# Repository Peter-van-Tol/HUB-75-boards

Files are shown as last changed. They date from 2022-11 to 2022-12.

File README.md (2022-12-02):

# HUB-75 boards

The HUB-75 boards is a collection of break-out boards (BOBs) for HUB-75 connnectors found on re-purposed FPGA cards such as the 5A-75B and 5A-75E. These cards can be picked up for 10\~20 dollars from China and form an ideal basis for tinkering with FPGAs. Based on these cheap FPGA's a project has been spraked, called Litex-CNC, which aims to repurpose these cards to a cheap CNC controller. CNC-machines normally have field power which is 12\~24V and thus the FPGA cannot direclty be connected to the components of the machine. Therefore a set of break-out boards have been developed for GPIO inputs/outputs, stepgen, encoders, etc.

## Design philosophy
> Why not a hat one might ask? This project offers more flexibility. By combining different break-out can be combined to suit the machine that is being built. A hat also comes with a larger risk in design errors; smaller boards are easier to design, produce and check.

All BOBs will have the same dimensions of 85 mm x 56 mm. This size is equal to that of the Raspberry Pi 4, however the mounting holes are placed on the four corners and thus different from the RPi. Getting the mounting holes at the same location as the RPi made the design much more difficult. Placement of the connectors also hampers stacking these boards on top of each other, so not being to able to stack them on top of a RPi seems permissible.

The outputs of the BOBs will be on the bottom edge (long side). Field power and logic power are provided from the left side of the board. The HUB-75 connectors will be placed on the top of the boards. This makes it easier to route the digital signals and high-power signals separately from each other in the cabinet.

The smalles trace and spacing is 0.2 mm. These boards are designed to be ordered from an online PCB manufacturer. Some desktop milling machines might have the accuracy to create these traces, so you might give it a try when you are feeling lucky. The smallest holes (vias) are 0.3 mm in size.

All components are selected to be hand-solderable. This means that the following minimum sizes SMD components will be used:
- resistors, LED's, capacitors: SMD-1206
- diodes: SOD-123
- FET, transistors: SOT-23

## HUB-75 pinout
Each connector has 6 individual pins (1, 2, 3, 5, 6, and 7) and 8 shared pins (8 through 15). The standard pin-out of a HUB-75 connector is shown below.

| HUB75 pin | Pin | Pin | HUB75 pin |
|---|---|---|---|
| R0 | 1 | 2 | G0 |
| B0 | 3 | 4 | *GND* |
| R1 | 5 | 6 | G1 |
| B1 | 7 | 8 | E |
| A | 9 | 10 | B |
| C | 11 | 12 | D |
| CLK | 13 | 14 | STB |
| OE | 15 | 16 | *GND* |

Each HUB-75 connector will use the individual pins and in special cases one of the shared pins. In the design it should be taken into account that boards which uses the same shared pins might be mutual exclusive when the functions are different (different types of stepgen BOBs can off course be combined.

## Available BOBs
The table below shows the BOBs which are currently available in this repository, along with their status.

| Category  | Name | Description | HUB-75 | Status |
|---|---|---|---|---|
| stepgen | [HUB75-Differential_stepgen](HUB75-Differential_stepgen) | 3 differential stepgen channels, frequency up to 400 kHz | 2 + 0.5 | Prototype-2 ordered | 
| GPIO-out  | [HUB75-Sourcing_output](HUB75-Sourcing_output) | 12 channel sourcing output (<1 kHz, 4 A per channel, 4 A total) | 2 | Prototype-2 ordered | 
| GPIO-in | [HUB75-Sinking_input](HUB75-Sinking_input) | 12 channel sinking input (< 1 kHz) | 2 | Untested |

## Connecting the BOBs to your FPGA
On both the 5A-75B and the 5A-75E the `74HC245T` buffers are hard-wired as outputs. To be able to use the HUB-75 boards which require an input (as seen from the FPGA) some modifications on the board are required. Of both boards different versiosn exist, so the components can be at a different location on your board. Below are the locations of the buffer on a 5A-75B V6.1 (front) and 5A-75E V6.0 (back).

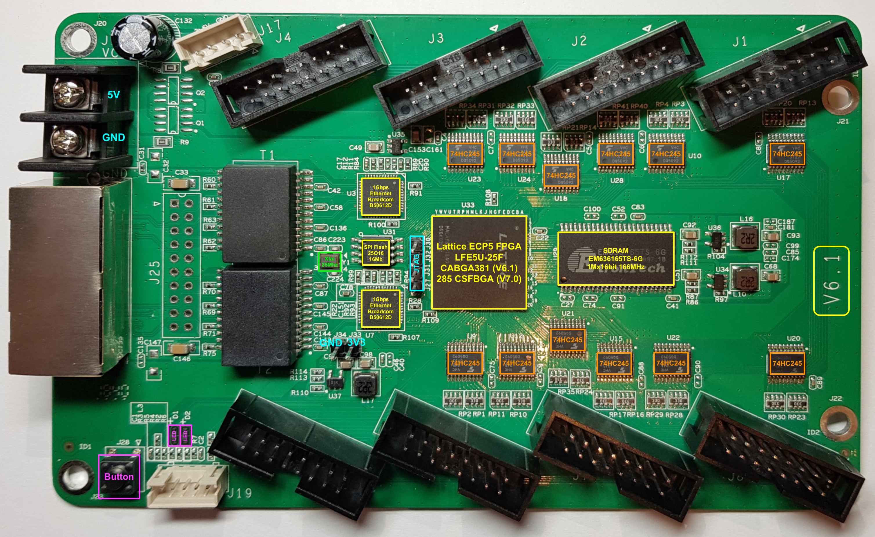
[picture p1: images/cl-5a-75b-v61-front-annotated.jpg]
5A-75B V6.1


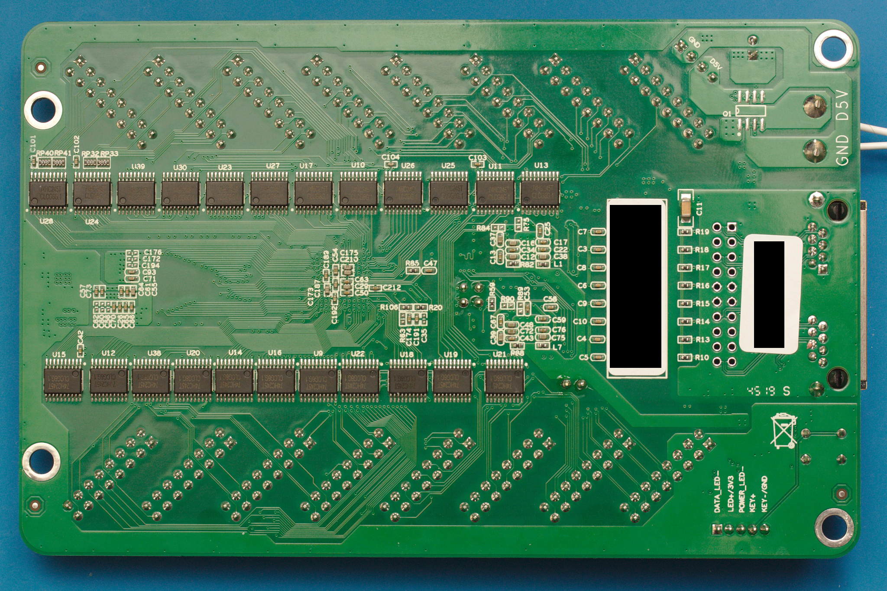
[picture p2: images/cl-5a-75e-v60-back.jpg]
5A-75E V6.0


Each buffer has 8 channels, while every HUB-75 connector has 6 individual pins. When you replace a buffer you will cahnge the behavior of one HUB-75 connector and partly that of its neighbor. All HUB-75 boards assume that a connector is either fully configured as input or as output. Therefore it is recommended to change the buffers direclty adjacent to each other, so the minimum amount of available connectors (partly input/ouput) are wasted.

The following changes have to be made to the buffers:
* De-solder the `74HC245T` buffer, this buffer cannot be re-used because its pins are not 5 Volt tolerant when `Vcc` is 3.3 Volt.
* Cut the trace to the pin `Vcc` (pin 20) and wire it to a 3.3V source (for example the JTAG-header). If you don't do this, a buffer configure as input will put 5 Volts on the pins of the FPGA, which will definately fry that pin or the whole board.
* Cut the trace to the pin `DIR` (pin 20) and wire it to a GND source to configure the buffer as input.
* Replace the buffer with a buffer with 5V tolerant inputs, such as the `74LVC245` ([datasheet](https://www.ti.com/lit/ds/symlink/sn74lvc245a.pdf)).

After these modifications the board might look a like this (on this particular board a single buffer has been replace, as it is a test-board for LitexCNC).

TODO: picture to be taken

## License 
The boards in this repository are licensed unde Creative Commons BY-NC-SA. This means you are allowed to:
* **Share** — copy and redistribute the material in any medium or format
* **Adapt** — remix, transform, and build upon the material

As long as:
* **Attribution** — You must give appropriate credit, provide a link to the license, and indicate if changes were made. You may do so in any reasonable manner, but not in any way that suggests the licensor endorses you or your use.
* **NonCommercial** — You may not use the material for  commercial purposes. Of course you can use the machine you created or modified using these boards for commercial purposes. 
* **ShareAlike** — If you remix, transform, or build upon the material, you must distribute your contributions under the  same license  as the original.

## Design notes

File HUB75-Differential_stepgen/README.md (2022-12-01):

# HUB-75 Differential stepgen
Break-out board with 3 stepgen channels. As most stepper motor drivers are opto-isolated, the board does not provide any extra isolation.

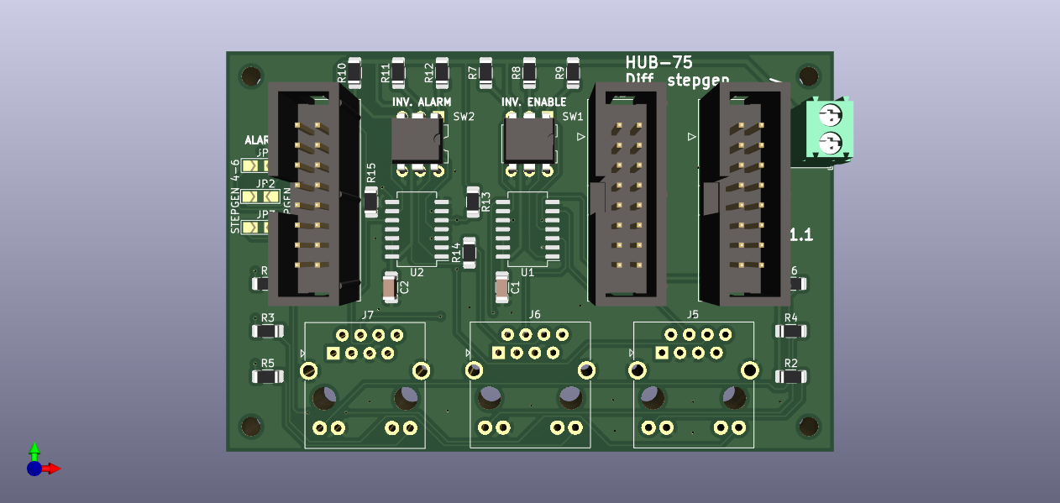
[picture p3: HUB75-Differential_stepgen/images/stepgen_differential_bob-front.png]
PCB front


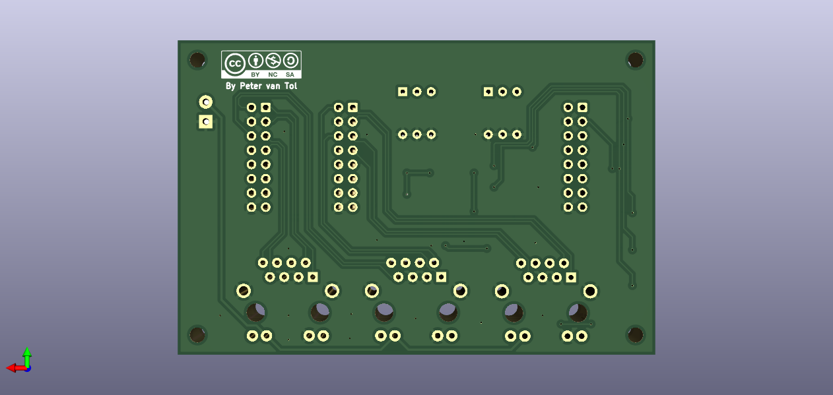
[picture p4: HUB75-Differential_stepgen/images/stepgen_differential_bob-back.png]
PCB back


> **NOTE** <br> On the images the RJ45-connectors and the SO-16 packages are not displayed as their models are not available in KiCAD.

## Features

- 2 HUB-75 input connectors
- 1 HUB-75 output connector for alarm
- 3 channel differential stepgen drivers using RJ-45 plugs with frequency up to 400 kHz
- status LEDs on RJ-45 plugs for Enable and Alarm
- selectable active HIGH or active LOW for Enable using dip-switches
- selectable active HIGH or active LOW for Alarm using dip-switches

Two differential stepgen BOBs can share HUB-75 output connector by setting the solder jumpers on the board for either stepgen 1-3 or stepgen 4-6.

## Applications

- Driving stepper motor drivers with internal opto-couplers.

> **NOTE** <br> To save on the number of outputs used, one can opt for a single ended version of the BOB.

## Example wiring

Any standard UTP-cable can be used for as a 'donor' for connecting the BOB to the driver. One can either:
- cut the cable and use the wires in the screw-terminals of the driver.
- create a small break-out board with RJ45 connector which fits your driver. The pitch *and* the order of the pins makes this a custom solution for almost any driver. These break-out boards, when developed, will be shared here as well, listed by type of the driver. These will be designed to be DIY, as small PCB's tend to be expensive.

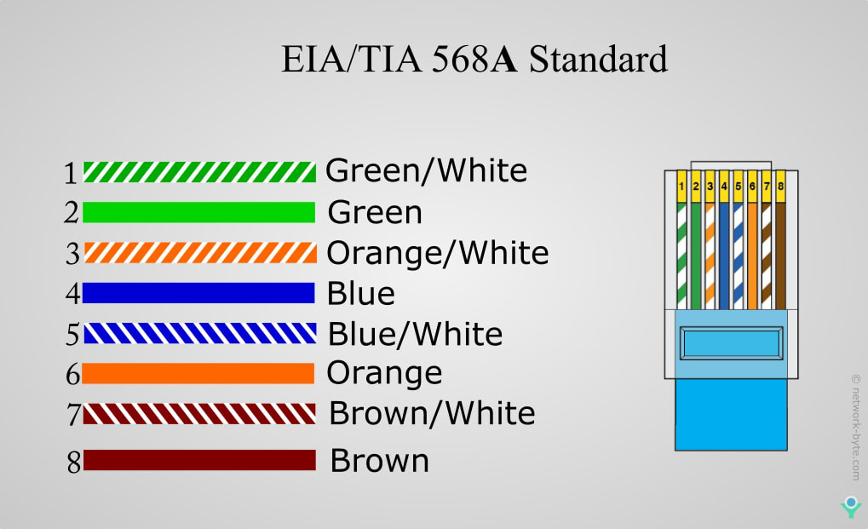
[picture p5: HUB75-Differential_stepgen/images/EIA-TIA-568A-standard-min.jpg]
EIA-TIA-568A-standard


The pin-out of the cable is as folllows

| RJ-45 pin | Color | Function | 
|---|---|---|
| 1 | green/white  | STEP- |
| 2 | green | STEP+ |
| 3 | orange/white | GND |
| 4 | blue | ENA |
| 5 | blue/white | GND |
| 6 | orange | ALARM |
| 7 | brown/white  | DIR- |
| 8 | brown | DIR+ |

## Litex-CNC example configuration
Let's assume that the two output HUB-745 connectors on this board are connected to J1 and J2 of the FPGA and the input connector is J16. To configure the pins for output, you can use the configuration-block below as a starting point. Optionaly the pin names can also be set in the configuration, making the HAL clearer.

``` json
{
    ...,
    "stepgen": [
        {
            "step_pin": "j1:0",
            "dir_pin": "j1:1",
            "soft_stop": true
        },
        {
            "step_pin": "j1:2",
            "dir_pin": "j1:4",
            "soft_stop": true
        }
        {
            "step_pin": "j1:5",
            "dir_pin": "j1:6",
            "soft_stop": true
        },
        {
            "step_pin": "j2:0",
            "dir_pin": "j2:1",
            "soft_stop": true
        },
        {
            "step_pin": "j2:2",
            "dir_pin": "j2:4",
            "soft_stop": true
        }
        {
            "step_pin": "j2:5",
            "dir_pin": "j2:6",
            "soft_stop": true
        }
    ],
    "gpio_in": [
        {"pin": "j16:0", "name": "stepgen.0.alarm"},
        {"pin": "j16:1", "name": "stepgen.1.alarm"},
        {"pin": "j16:2", "name": "stepgen.2.alarm"},
        {"pin": "j16:4", "name": "stepgen.3.alarm"},
        {"pin": "j16:5", "name": "stepgen.4.alarm"},
        {"pin": "j16:6", "name": "stepgen.5.alarm"},
    ],
    "gpio_in": [
        {"pin": "j1:14", "name": "stepgen.enable"},
    ],
    ...
}
```

> **NOTE** <br> The BOB uses pin 14 (`OE`) of the HUB-75 connector, which is a shared pin. This board therefore cannot be used in combination with other BOB's using the same pin when it's function is incompatible.

## Bill of materials
The table below gives the bill of materials used for this BOB and an indication of its price. The list is available as public list for the following companies:
* [Reichtelt](https://www.reichelt.de/my/1997667). This is non-affiliate link, I do not earn any money when you order this list from this specific vendor, nor the vendor endorses this project. Reichtelt is a supplyer for Western Europe.

When you order with Mouser or antohter supplier, please share a list here.

| Part. number | Package | Description | Datasheet | Amount | Price*  |
|---|---|---|---|---|---|
| 74HC86 | SO-16 | Quad XOR-gates | | 2 | € 0.16  |
| SMD 1/4W270 | SMD 1206  | Resistor, 270 Ohm | | 6 | € 0.03  |
| SMD 1/4W 10K | SMD 1206  | Resistor, 10 kOhm | | 12 | € 0.03  |
| X7R-G1206 100N | SMD 1206  | Capacittor 100 nF | | 12 | € 0.22  | 
| DIP 3P | DIP-6 | DIP-switch, 3P | | 2 | € 0.33  |
| DG250 3,5-2 | - | Screw/spring terminal 2.5 mm pitch | | 1 | € 0.22  |
| BOX 2X8 | - | Box header 2x8, 2.54 mm pitch | | 3 | € 0.16  |
| CAT5 | - | RJ-45 Bus with LED** | | 3 | € 1.07  |

**NOTES**: 
1. The price is based on availability in the Netherlands with a single shop for all parts. Parts might be sourced cheaper depending on your location, available sources and the time you want to wait before receiving the components.
2. When using a different source for the connector, please verify the footprint, as there are many variants.

## Known issues

This board does not have any known issues yet.

If you find any issue, please file a bug using GitHub.

# Version history

**1.1**
* Changed HUB75 connectors from pin headers to IDC connectors (shrouded). Moved several components to make space for the larger footprint
* Wired alarm 1-3 to pin 1-3 of J3 (was pin 3-5-7, which was not logical for config). Wired alarm 4-6 to pin 5-7 of J3 (NOTE: pin 4 is GND). Version 1.0 boards cannot be connected to version 1.1 boards due to this change.
* Added labels to clarify the function of the DIP-switches and solder jumpers. 

**1.0**
* Initial version for proto-type.

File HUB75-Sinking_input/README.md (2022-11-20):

# HUB-75 Sinking input 
Break-out board with 12 channel sinking input. The FPGA is galvanically separated from field power using opto-couplers.

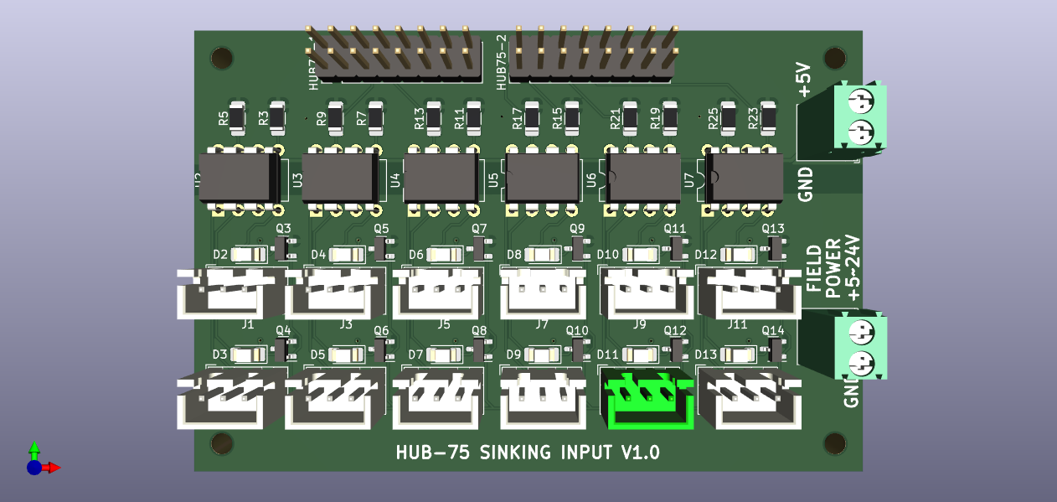
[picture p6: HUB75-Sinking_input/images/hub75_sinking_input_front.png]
PCB front


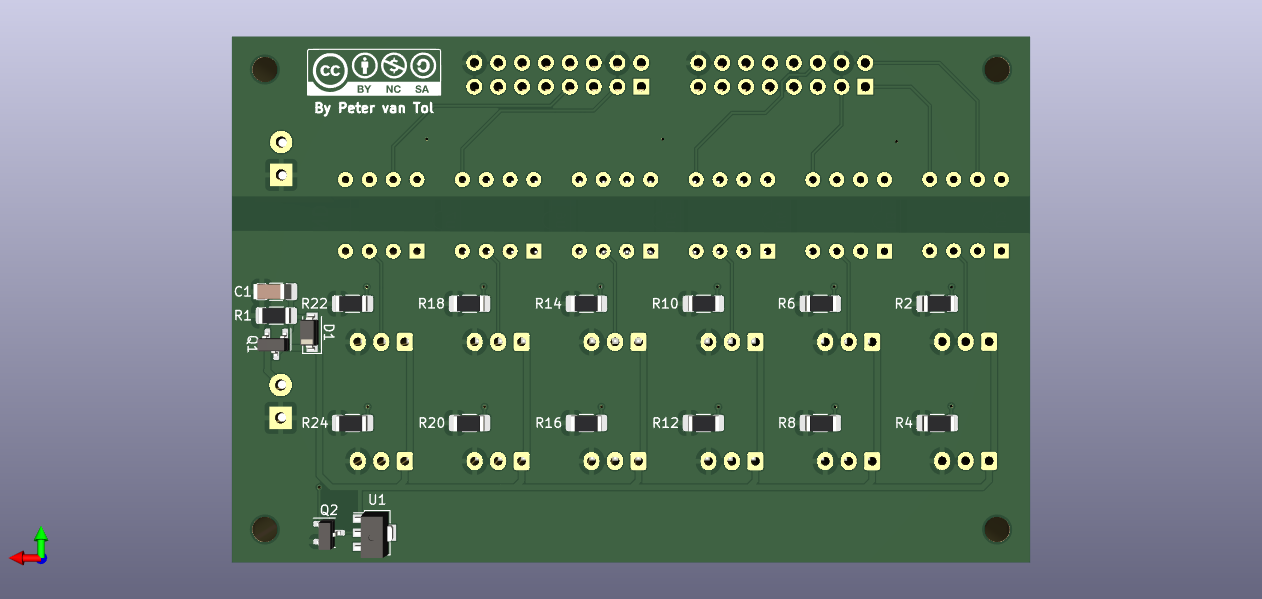
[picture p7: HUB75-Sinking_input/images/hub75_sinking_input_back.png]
PCB back


## Features

- 2 HUB-75 output connectors
- 12 channel sinking output using JST connectors
- 5\~24 V Field power with reverse polarity protection
- indicating LED for each output
- indicated switching frequency 1 kHz

## Applications

- PNP (souring) limit switches
- Momentary push-buttons
- Slow encoders, for example for user input

> **NOTE** <br> The `PC827` optocouplers have a maximum rated frequency of 80 kHz. It is recommended to start at a frequency of 1 kHz and work up from there.

## Example wiring

TODO: example

## Litex-CNC example configuration
Let's assume that the two HUB-745 connectors on this board are connected to J15 and J16 of the FPGA. To configure the pins for output, you can use the configuration-block below as a starting point. Optionaly the pin names can also be set in the configuration, making the HAL clearer.

``` json
{
    ...,
    "gpio_in": [
        {"pin": "j15:0"},
        {"pin": "j15:1"},
        {"pin": "j15:2"},
        {"pin": "j15:4"},
        {"pin": "j15:5"},
        {"pin": "j15:6"},
        {"pin": "j16:0"},
        {"pin": "j16:1"},
        {"pin": "j16:2"},
        {"pin": "j16:4"},
        {"pin": "j16:5"},
        {"pin": "j16:6"}
    ],
    ...
}
```

Alternatively, the BOB can also be used for PWM output. In that case the configuration may look something like below. In this example it is assumed that outputs on J16 are used for three encoders.

``` json
{
    ...,
    "encoders": [
        {  
            "pin_A":"j16:0",
            "pin_B":"j16:1"
        },
        {  
            "pin_A":"j16:2",
            "pin_B":"j16:4"
        },
        {  
            "pin_A":"j16:5",
            "pin_B":"j16:6"
        }
    ],
    ...
}
```

## Bill of materials

The table below gives the bill of materials used for this BOB and an indication of its price. The list is available as public list for the following companies:
* [Reichtelt](https://www.reichelt.de/my/1998173). This is non-affiliate link, I do not earn any money when you order this list from this specific vendor, nor the vendor endorses this project. Reichtelt is a supplyer for Western Europe.

When you order with Mouser or antohter supplier, please share a list here.

| Part. number | Package | Description | Datasheet | Amount | Price*  |
|---|---|---|---|---|---|
| LTV827 | DIP-8 | Dual-channel opto-coupler | | 6 | € 0.31  |
| AO3401A | SOT-23 | P-Channel MOSFET, 30V | | 1 | € 0.25  |
| ZENER 12V | SOT-23 | 12V Zener diode*** | | 1 | € 0.05  |
| 4.7K | SMD 1206  | Resistor, 4.7 kOhm | | 12 | € 0.03  |
| 10K | SMD 1206  | Resistor, 10 kOhm | | 1 | € 0.03  |
| LED | SMD 1206  | LED, green, If > 20 mA | | 12 | € 0.08  |
| CAP 15N | SMD 1206  | Capitor, 15 nF | | 1 | € 0.02  |
| JST XH 3P | - | JST XH conn. 2.5 mm pitch | | 12 | € 0.15  |
| DG250 3,5-2  | - | Screw/spring terminal 2.5 mm pitch | | 2 | € 0.22  |
| BOX 2X8 | - | Box header 2x8, 2.54 mm pitch | | 2 | € 0.16  |
| 2N7002** | SOT-23 | N-Channel MOSFET (current mirror)  | | 13 | € 0.04  |
| CL2N8-G** | SOT-89 | LED-driver 20 mA (current mirror)  | | 1 | € 0.39  |
| R** | SMD 1206  | Resistor, TBD Ohm (alternative) | | 12 | € 0.03  |

**NOTES**: 
1. The price is based on availability in the Netherlands with a single shop for all parts. Parts might be sourced cheaper depending on your location, available sources and the time you want to wait before receiving the components.
2. The components `CL2N8-G` and `2N7002` form a current mirror for driving the status LEDs. This current mirror can be replaced with a fixed resistor `R`, which should be calculated based on the voltage used for Field power.
3. The zener diode is only required when Field Power is >12 Volt for protecting the MOSFETs.

## Known issues

This board does not have any known issues yet.

If you find any issue, please file a bug using GitHub.

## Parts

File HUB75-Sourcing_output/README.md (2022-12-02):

# HUB-75 Sourcing output 
Break-out board with 12 channel sourcing output. The FPGA is galvanically separated from field power using opto-couplers. To enhance the power each channel can deliver, the loads are being switched with a MOSfet (`AO3401A`). 

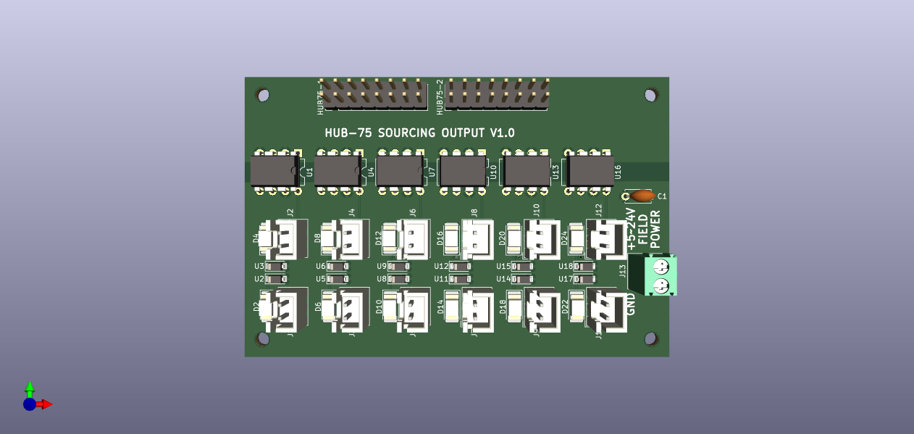
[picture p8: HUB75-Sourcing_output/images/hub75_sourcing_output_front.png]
PCB front


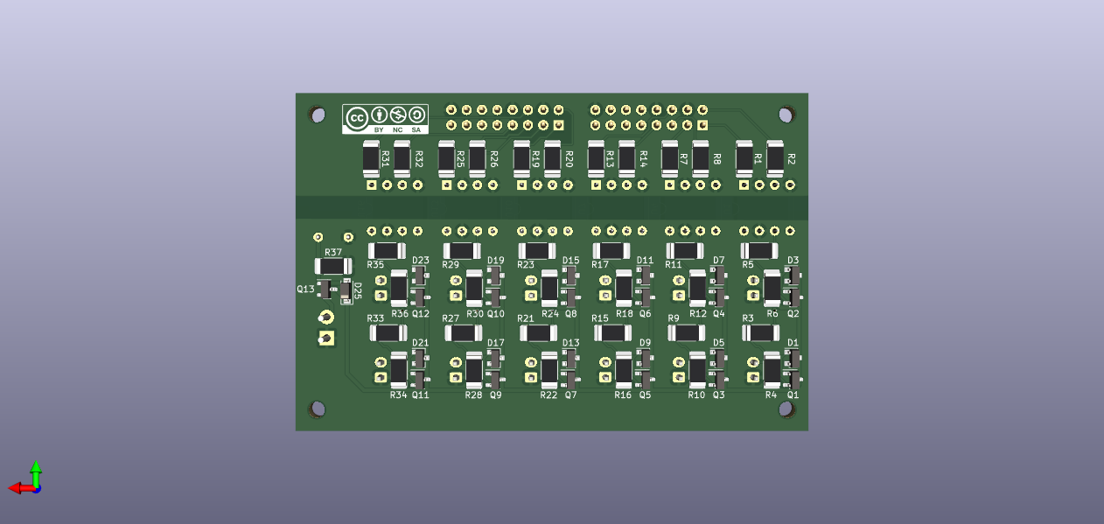
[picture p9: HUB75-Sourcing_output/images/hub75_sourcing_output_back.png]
PCB back


## Features

- 2 HUB-75 input connectors
- 12 channel sourcing output using JST connectors
- 5\~24 V Field power with reverse polarity protection
- rated 300 mA power per channel
- indicating LED for each output
- indicated switching frequency 1 kHz

## Applications

- Driving LEDs (optional dimmable by using PWM)
- Driving solenoids with current lower then rated current
- Driving relays for larger loads 

> **NOTE** <br> The `PC827` optocouplers have a maximum rated frequency of 80 kHz. When using this board in combination with PWM, the chosen frequency should be well below this limit. It is recommended to start at a frequency of 1 kHz and work up from there. PDM with LitexCNC will not work with this board, because the frequency cannot be set and will be too high. 

## Example wiring

TODO: example

> **NOTE** <br> When connecting any inductive loads, please connect a fly-back diode!

## Litex-CNC example configuration
Let's assume that the two HUB-745 connectors on this board are connected to J1 and J2 of the FPGA. To configure the pins for output, you can use the configuration-block below as a starting point. Optionaly the pin names can also be set in the configuration, making the HAL clearer.

``` json
{
    ...,
    "gpio_out": [
        {"pin": "j1:0"},
        {"pin": "j1:1"},
        {"pin": "j1:2"},
        {"pin": "j1:4"},
        {"pin": "j1:5"},
        {"pin": "j1:6"},
        {"pin": "j2:0"},
        {"pin": "j2:1"},
        {"pin": "j2:2"},
        {"pin": "j2:4"},
        {"pin": "j2:5"},
        {"pin": "j2:6"}
    ],
    ...
}
```

Alternatively, the BOB can also be used for PWM output. In that case the configuration may look something like below. In this example it is assumed that outputs J10 through J12 on the BOB are used for PWM.

``` json
{
    ...,
    "gpio_out": [
        {"pin": "j1:0"},
        {"pin": "j1:1"},
        {"pin": "j1:2"},
        {"pin": "j1:4"},
        {"pin": "j1:5"},
        {"pin": "j1:6"},
        {"pin": "j2:0"},
        {"pin": "j2:1"},
        {"pin": "j2:2"}
    ],
    "pwm": [
        {"pin": "j2:4"},
        {"pin": "j2:5"},
        {"pin": "j2:6"}
    ]
    ...
}
```

When using PWM, the HAL pin `pwm.###.pwm_freq` should be set to a value smaller then 1000 (1 kHz). Higher frequencies can be tested using the board, by increasing this value. The uppper limit is 80 kHz, which is the maximum frequency of the `PC817` opto-coupler. 

## Bill of materials

The table below gives the bill of materials used for this BOB and an indication of its price. The list is available as public list for the following companies:
* [Reichtelt](https://www.reichelt.de/my/1997628). This is non-affiliate link, I do not earn any money when you order this list from this specific vendor, nor the vendor endorses this project. Reichtelt is a supplyer for Western Europe.

When you order with Mouser or antohter supplier, please share a list here.

| Part. number | Package | Description | Datasheet | Amount | Price*  |
|---|---|---|---|---|---|
| LTV827 | DIP-8 | Dual-channel opto-coupler | | 6 | € 0.31  |
| AO3401A | SOT-23 | P-Channel MOSFET, 30V | | 13 | € 0.25  |
| ZENER 12V | SOT-23 | 12V Zener diode*** | | 13 | € 0.05  |
| 200R | SMD 1206  | Resistor, 200 Ohm | | 12 | € 0.03  |
| 240 | SMD 1206  | Resistor, 240 Ohm | | 12 | € 0.03  |
| 10K | SMD 1206  | Resistor, 10 kOhm | | 13 | € 0.03  |
| LED | SMD 1206  | LED, green, If > 20 mA | | 12 | € 0.08  |
| CAP 15N | SMD 1206  | Capitor, 15 nF | | 1 | € 0.02  |
| JST XH 2P | - | JST XH conn. 2.5 mm pitch | | 12 | € 0.15  |
| DG250 3,5-2  | - | Screw/spring terminal 2.5 mm pitch | | 1 | € 0.22  |
| BOX 2X8 | - | Box header 2x8, 2.54 mm pitch | | 2 | € 0.16  |
| 2N7002** | SOT-23 | N-Channel MOSFET (current mirror)  | | 13 | € 0.04  |
| CL2N8-G** | SOT-89 | LED-driver 20 mA (current mirror)  | | 1 | € 0.39  |
| R** | SMD 1206  | Resistor, TBD Ohm (alternative) | | 12 | € 0.03  |

**NOTES**: 
1. The price is based on availability in the Netherlands with a single shop for all parts. Parts might be sourced cheaper depending on your location, available sources and the time you want to wait before receiving the components.
2. The components `CL2N8-G` and `2N7002` form a current mirror for driving the status LEDs. This current mirror can be replaced with a fixed resistor `R`, which should be calculated based on the voltage used for Field power.
3. The zener diode is only required when Field Power is >12 Volt for protecting the MOSFETs.

## Known issues

- The reverse voltage protection uses a footprint for the resistor which is too large in the prototype (component not available). In the next version this footprint is modified to the default SMD 1206. Also the cpacitor is a through-hole component, as the value was wrong. The value is corrected in the BOM. In the next version this component is also replaced to SMD 1206.
- Current mirror is to be tested whether it works reliable.

If you find more issues, please file a bug using GitHub.

# Version history

**1.1**
* Corrected P-channel MOSFET's, the source and drain where switched, which prevented the V1.0 board from working. 
* Changed pin-headers to IDC-headers. Rerouted because of more space required by the IDC-header
* Corrected footprint of reverse current protection. Added jumper to be able to by-pass this circuit. 

**1.0**
* Initial version for proto-type.

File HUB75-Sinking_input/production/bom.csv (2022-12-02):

Designator | Footprint | Quantity | Value | LCSC Part #
C1 | C_1206_3216Metric_Pad1.33x1.80mm_HandSolder | 1 | 15nF
D1 | D_SOT-23_ANK | 1 | D_Zener
D10, D11, D12, D13, D2, D3, D4, D5, D6, D7, D8, D9 | LED_1206_3216Metric_Pad1.42x1.75mm_HandSolder | 12 | LED_Small
HUB75-1, HUB75-2 | IDC-Header_2x08_P2.54mm_Vertical | 2 | Conn_02x08_Odd_Even
J1, J10, J11, J12, J2, J3, J4, J5, J6, J7, J8, J9 | JST_XH_B3B-XH-A_1x03_P2.50mm_Vertical | 12 | Conn_01x03_Male
JP1 | SolderJumper-2_P1.3mm_Open_TrianglePad1.0x1.5mm | 1 | Jumper_2_Open
PWR1, PWR2 | TerminalBlock_Phoenix_PT-1,5-2-3.5-H_1x02_P3.50mm_Horizontal | 2 | Screw_Terminal_01x02
Q1 | SOT-23 | 1 | AO3401A
Q10, Q11, Q12, Q13, Q14, Q2, Q3, Q4, Q5, Q6, Q7, Q8, Q9 | SOT-23 | 13 | 2N7002
R1 | R_1206_3216Metric_Pad1.30x1.75mm_HandSolder | 1 | 10K
R10, R12, R14, R16, R18, R2, R20, R22, R24, R4, R6, R8 | R_1206_3216Metric_Pad1.30x1.75mm_HandSolder | 12 | R
R11, R13, R15, R17, R19, R21, R23, R25, R3, R5, R7, R9 | R_1206_3216Metric_Pad1.30x1.75mm_HandSolder | 12 | 4.7K
U1 | SOT-89-3 | 1 | CL2N8-G
U2, U3, U4, U5, U6, U7 | DIP-8_W7.62mm | 6 | LTV-827

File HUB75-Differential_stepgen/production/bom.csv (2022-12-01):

Designator | Footprint | Quantity | Value | LCSC Part #
C1, C2 | C_1206_3216Metric_Pad1.33x1.80mm_HandSolder | 2 | 100nF
J1, J2, J3 | IDC-Header_2x08_P2.54mm_Vertical | 3 | Conn_02x08_Odd_Even
J4 | TerminalBlock_Phoenix_PT-1,5-2-3.5-H_1x02_P3.50mm_Horizontal | 1 | Screw_Terminal_01x02
J5, J6, J7 | RJ45_BEL_SS74301-00x_Vertical | 3 | RJ45_LED
JP1, JP2, JP3 | SolderJumper-3_P2.0mm_Open_TrianglePad1.0x1.5mm_NumberLabels | 3 | SolderJumper_3_Bridged123
R1, R2, R3, R4, R5, R6 | R_1206_3216Metric_Pad1.30x1.75mm_HandSolder | 6 | 270
R10, R11, R12, R13, R14, R15, R7, R8, R9 | R_1206_3216Metric_Pad1.30x1.75mm_HandSolder | 9 | 10k
SW1, SW2 | DIP-6_W7.62mm | 2 | SW_DIP_x03
U1, U2 | SO-14_5.3x10.2mm_P1.27mm | 2 | 74HC86

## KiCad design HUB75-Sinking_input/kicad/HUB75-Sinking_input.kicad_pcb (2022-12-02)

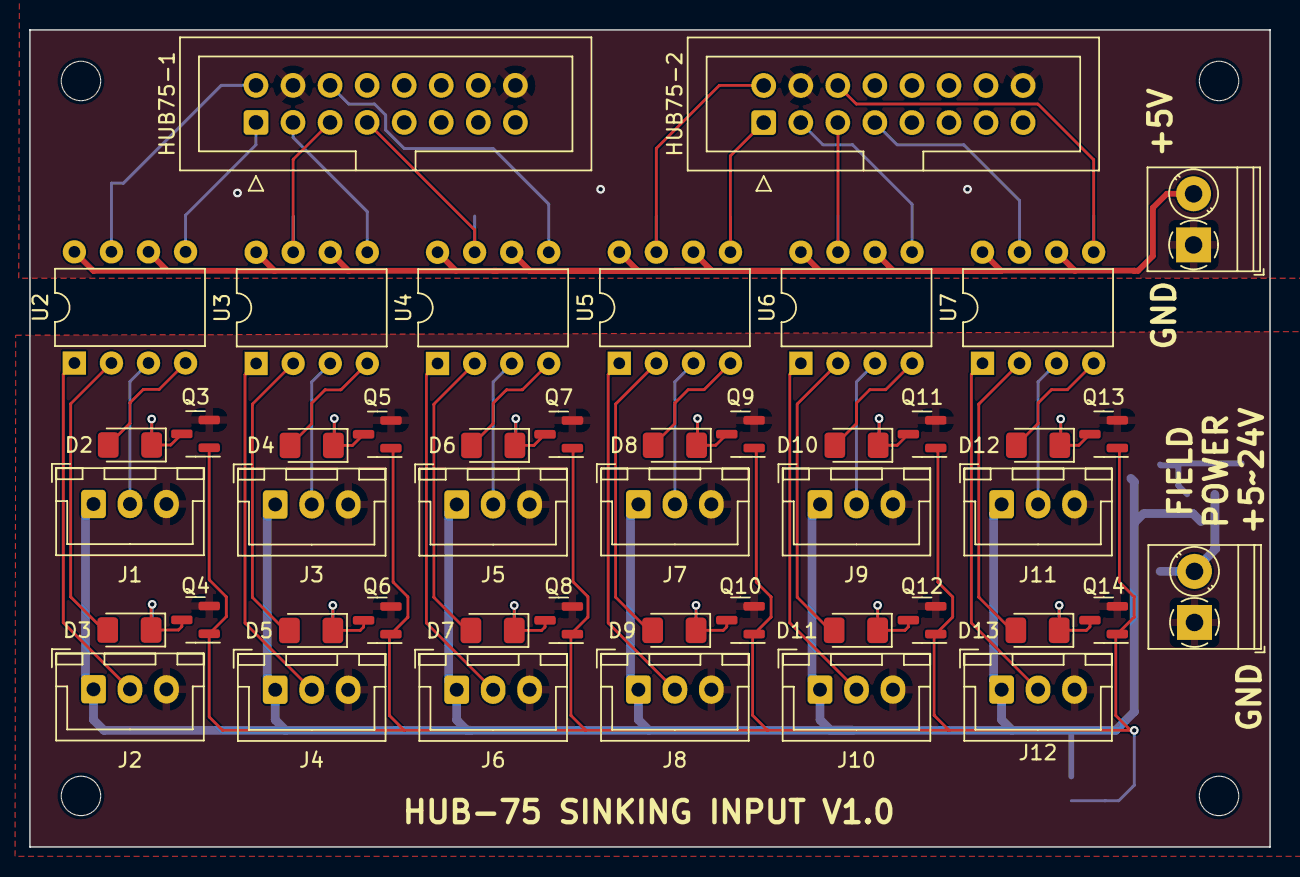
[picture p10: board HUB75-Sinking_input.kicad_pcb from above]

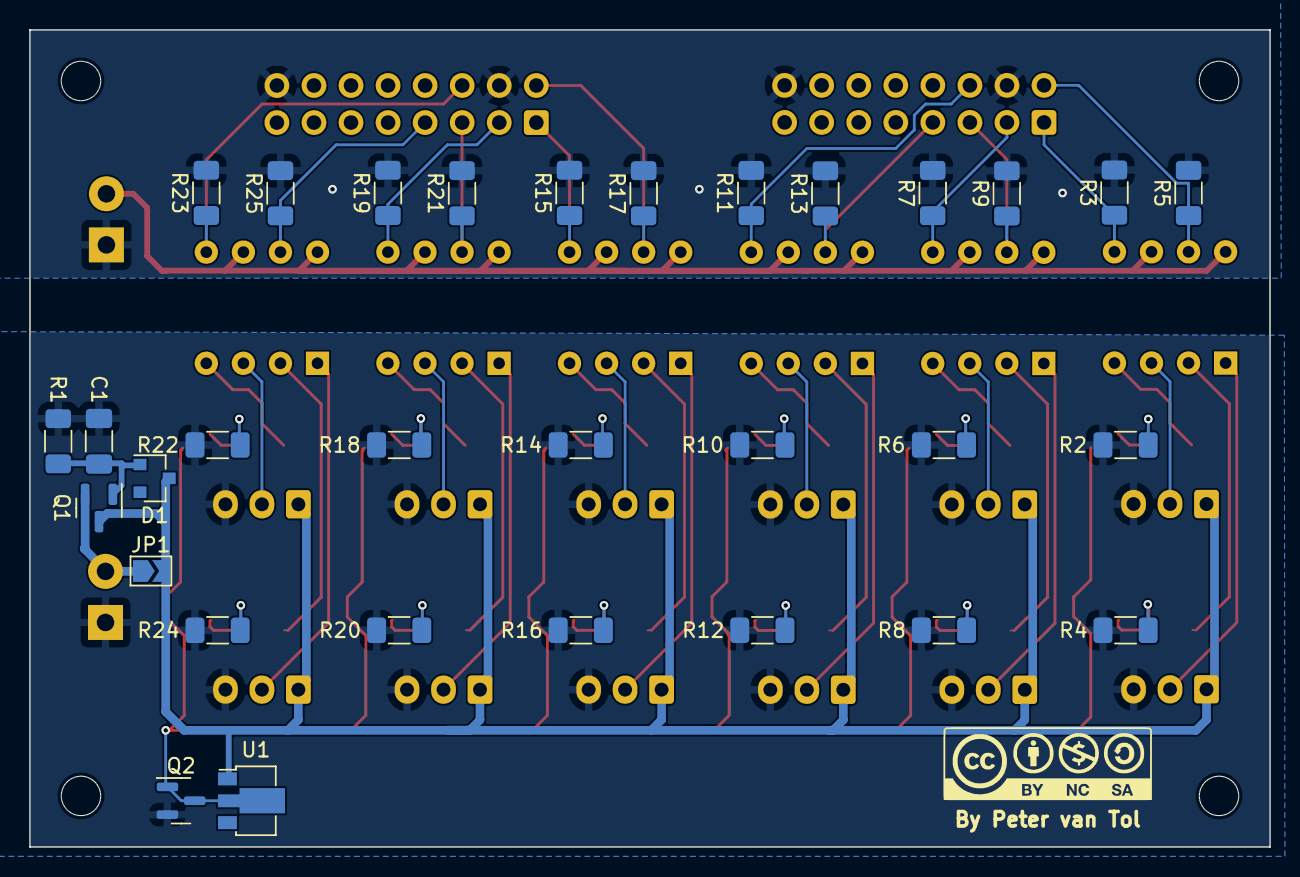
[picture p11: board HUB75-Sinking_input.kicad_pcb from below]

Board: 2 copper layers, 85.0 x 56.0 mm, 81 parts (31 on the bottom side), 55 nets.

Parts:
C1: 15nF; C_1206_3216Metric_Pad1.33x1.80mm_HandSolder
D1: D_Zener; D_SOT-23_ANK
D2, D3, D4, D5, D6, D7, D8, D9, D10, D11, D12, D13: LED_Small; LED_1206_3216Metric_Pad1.42x1.75mm_HandSolder
HOLE1, HOLE2, HOLE3, HOLE4: MountingHole_2.7mm_M2.5_DIN965
HUB75-1, HUB75-2: Conn_02x08_Odd_Even; IDC-Header_2x08_P2.54mm_Vertical
J1, J2, J3, J4, J5, J6, J7, J8, J9, J10, J11, J12: Conn_01x03_Male; JST_XH_B3B-XH-A_1x03_P2.50mm_Vertical
JP1: Jumper_2_Open; SolderJumper-2_P1.3mm_Open_TrianglePad1.0x1.5mm
PWR1, PWR2: Screw_Terminal_01x02; TerminalBlock_Phoenix_PT-1,5-2-3.5-H_1x02_P3.50mm_Horizontal
Q1: AO3401A; SOT-23
Q2, Q3, Q4, Q5, Q6, Q7, Q8, Q9, Q10, Q11, Q12, Q13, Q14: 2N7002; SOT-23
R1: 10K; R_1206_3216Metric_Pad1.30x1.75mm_HandSolder
R2, R4, R6, R8, R10, R12, R14, R16, R18, R20, R22, R24: R; R_1206_3216Metric_Pad1.30x1.75mm_HandSolder
R3, R5, R7, R9, R11, R13, R15, R17, R19, R21, R23, R25: 4.7K; R_1206_3216Metric_Pad1.30x1.75mm_HandSolder
U1: CL2N8-G; SOT-89-3
U2, U3, U4, U5, U6, U7: LTV-827; DIP-8_W7.62mm

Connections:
+5V: PWR2.2, U2.6, U2.8, U3.6, U3.8, U4.6, U4.8, U5.6, U5.8, U6.6, U6.8, U7.6, U7.8
CUR_MIRROR: Q2.1 (G), Q2.3 (D), Q3.1 (G), Q4.1 (G), Q5.1 (G), Q6.1 (G), Q7.1 (G), Q8.1 (G), Q9.1 (G), Q10.1 (G), Q11.1 (G), Q12.1 (G), Q13.1 (G), Q14.1 (G), U1.2 (GND)
GND: HUB75-1.4, HUB75-1.16, HUB75-2.4, HUB75-2.16, PWR2.1, R3.2, R5.2, R7.2, R9.2, R11.2, R13.2, R15.2, R17.2, R19.2, R21.2, R23.2, R25.2
GNDD: C1.2, J1.3, J2.3, J3.3, J4.3, J5.3, J6.3, J7.3, J8.3, J9.3, J10.3, J11.3, J12.3, PWR1.1, Q2.2 (S), Q3.2 (S), Q4.2 (S), Q5.2 (S), Q6.2 (S), Q7.2 (S), Q8.2 (S), Q9.2 (S), Q10.2 (S), Q11.2 (S), Q12.2 (S), Q13.2 (S), Q14.2 (S), R1.2, R2.1, R4.1, R6.1, R8.1, R10.1, R12.1, R14.1, R16.1, R18.1, R20.1, R22.1, R24.1
GPIO1-1: HUB75-1.1, R3.1, U2.5
GPIO1-2: HUB75-1.2, R5.1, U2.7
GPIO1-3: HUB75-1.3, R7.1, U3.5
GPIO1-4: HUB75-1.5, R9.1, U3.7
GPIO1-5: HUB75-1.6, R11.1, U4.5
GPIO1-6: HUB75-1.7, R13.1, U4.7
GPIO2-1: HUB75-2.1, R15.1, U5.5
GPIO2-2: HUB75-2.2, R17.1, U5.7
GPIO2-3: HUB75-2.3, R19.1, U6.5
GPIO2-4: HUB75-2.5, R21.1, U6.7
GPIO2-5: HUB75-2.6, R23.1, U7.5
GPIO2-6: HUB75-2.7, R25.1, U7.7
unnamed: C1.1, D1.2 (A), Q1.1 (G), R1.1
unnamed: D2.1 (K), Q3.3 (D), R2.2
unnamed: D2.2 (A), U2.4
unnamed: D3.1 (K), Q4.3 (D), R4.2
unnamed: D3.2 (A), U2.2
unnamed: D4.1 (K), Q5.3 (D), R6.2
unnamed: D4.2 (A), U3.4
unnamed: D5.1 (K), Q6.3 (D), R8.2
unnamed: D5.2 (A), U3.2
unnamed: D6.1 (K), Q7.3 (D), R10.2
unnamed: D6.2 (A), U4.4
unnamed: D7.1 (K), Q8.3 (D), R12.2
unnamed: D7.2 (A), U4.2
unnamed: D8.1 (K), Q9.3 (D), R14.2
unnamed: D8.2 (A), U5.4
unnamed: D9.1 (K), Q10.3 (D), R16.2
unnamed: D9.2 (A), U5.2
unnamed: D10.1 (K), Q11.3 (D), R18.2
unnamed: D10.2 (A), U6.4
unnamed: D11.1 (K), Q12.3 (D), R20.2
unnamed: D11.2 (A), U6.2
unnamed: D12.1 (K), Q13.3 (D), R22.2
unnamed: D12.2 (A), U7.4
unnamed: D13.1 (K), Q14.3 (D), R24.2
unnamed: D13.2 (A), U7.2
unnamed: J1.2, U2.3
unnamed: J2.2, U2.1
unnamed: J3.2, U3.3
unnamed: J4.2, U3.1
unnamed: J5.2, U4.3
unnamed: J6.2, U4.1
unnamed: J7.2, U5.3
unnamed: J8.2, U5.1
unnamed: J9.2, U6.3
unnamed: J10.2, U6.1
unnamed: J11.2, U7.3
unnamed: J12.2, U7.1
unnamed: JP1.1 (A), PWR1.2, Q1.2 (S)
VDD: D1.1 (K), J1.1, J2.1, J3.1, J4.1, J5.1, J6.1, J7.1, J8.1, J9.1, J10.1, J11.1, J12.1, JP1.2 (B), Q1.3 (D), U1.1 (VDD)

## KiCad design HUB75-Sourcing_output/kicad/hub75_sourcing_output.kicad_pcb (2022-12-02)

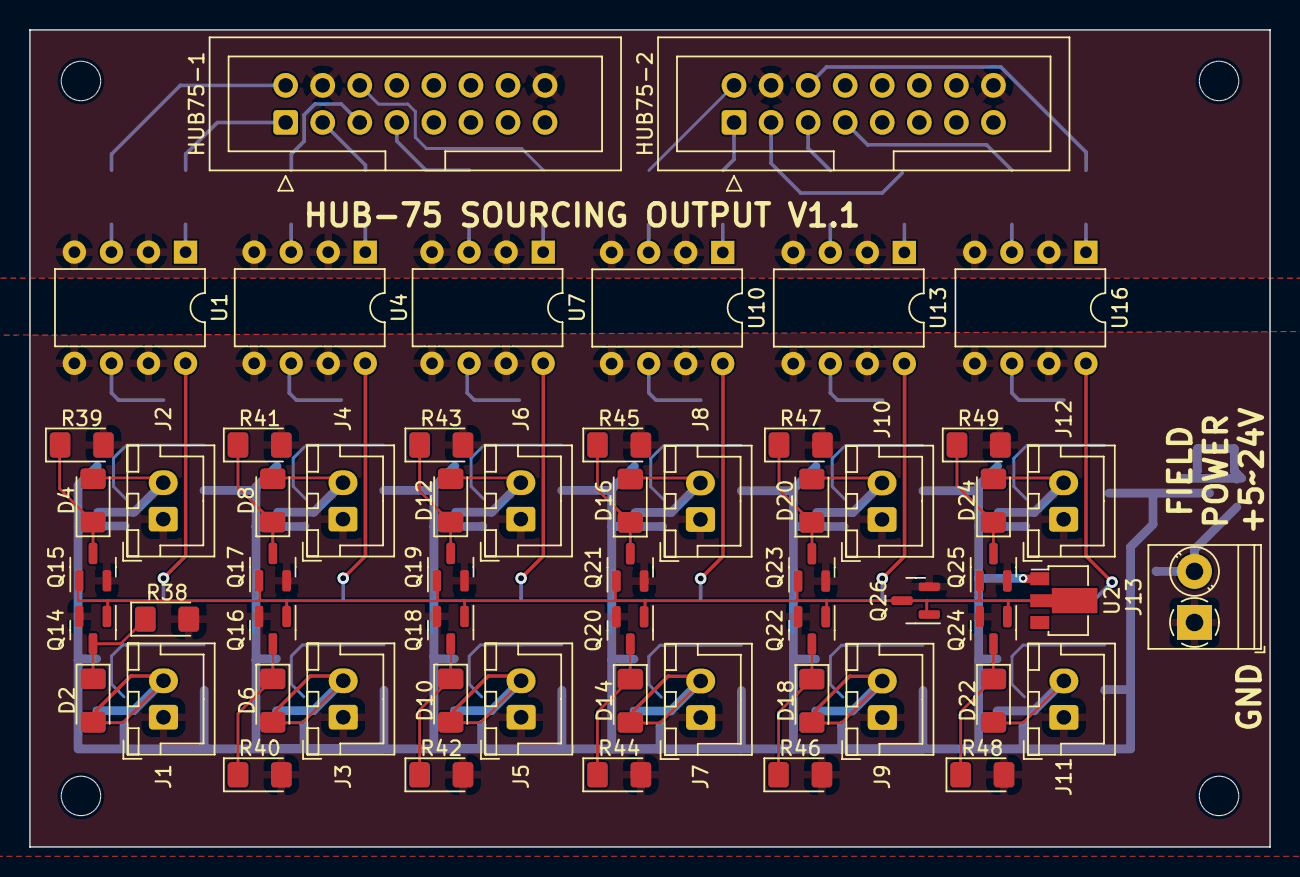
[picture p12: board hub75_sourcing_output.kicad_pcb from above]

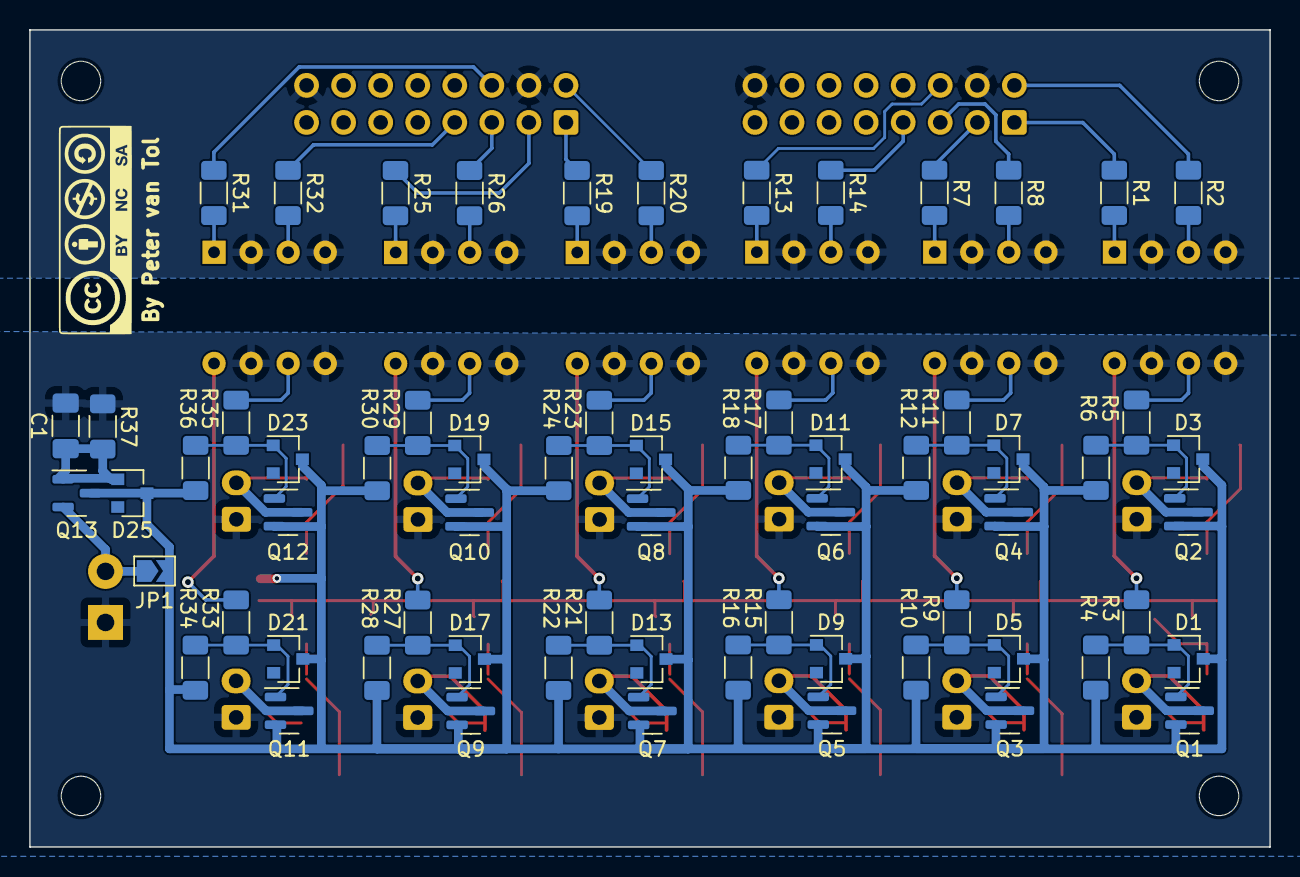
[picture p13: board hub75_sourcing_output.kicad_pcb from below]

Board: 2 copper layers, 85.0 x 56.0 mm, 128 parts (65 on the bottom side), 78 nets.

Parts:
C1: 15uF; C_1206_3216Metric_Pad1.33x1.80mm_HandSolder
D1, D3, D5, D7, D9, D11, D13, D15, D17, D19, D21, D23, D25: D_Zener; D_SOT-23_ANK
D2, D4, D6, D8, D10, D12, D14, D16, D18, D20, D22, D24: LED_Small; LED_1206_3216Metric_Pad1.42x1.75mm_HandSolder
HOLE1, HOLE2, HOLE3, HOLE4: MountingHole_2.7mm_M2.5_DIN965
HUB75-1, HUB75-2: Conn_02x08_Odd_Even; IDC-Header_2x08_P2.54mm_Vertical
J1, J2, J3, J4, J5, J6, J7, J8, J9, J10, J11, J12: Conn_01x02_Male; JST_XH_B2B-XH-A_1x02_P2.50mm_Vertical
J13: Screw_Terminal_01x02; TerminalBlock_Phoenix_PT-1,5-2-3.5-H_1x02_P3.50mm_Horizontal
JP1: Jumper_2_Open; SolderJumper-2_P1.3mm_Open_TrianglePad1.0x1.5mm
Q1, Q2, Q3, Q4, Q5, Q6, Q7, Q8, Q9, Q10, Q11, Q12: BSS84; SOT-23
Q13: AO3401A; SOT-23
Q14, Q15, Q16, Q17, Q18, Q19, Q20, Q21, Q22, Q23, Q24, Q25, Q26: 2N7002; SOT-23
R1, R2, R7, R8, R13, R14, R19, R20, R25, R26, R31, R32: 240R; R_1206_3216Metric_Pad1.30x1.75mm_HandSolder
R3, R5, R9, R11, R15, R17, R21, R23, R27, R29, R33, R35: 200R; R_1206_3216Metric_Pad1.30x1.75mm_HandSolder
R4, R6, R10, R12, R16, R18, R22, R24, R28, R30, R34, R36, R37: 10K; R_1206_3216Metric_Pad1.30x1.75mm_HandSolder
R38, R39, R40, R41, R42, R43, R44, R45, R46, R47, R48, R49: R; LED_1206_3216Metric_Pad1.42x1.75mm_HandSolder
U1, U4, U7, U10, U13, U16: LTV-827; DIP-8_W7.62mm
U2: CL2N8-G; SOT-89-3

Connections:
/opto_coupler_channel1/FET-driver1/SIGNAL_IN: R9.2, U4.8
/opto_coupler_channel1/FET-driver2/SIGNAL_IN: R11.2, U4.6
/opto_coupler_channel2/FET-driver1/SIGNAL_IN: R15.2, U7.8
/opto_coupler_channel2/FET-driver2/SIGNAL_IN: R17.2, U7.6
/opto_coupler_channel3/FET-driver1/SIGNAL_IN: R21.2, U10.8
/opto_coupler_channel3/FET-driver2/SIGNAL_IN: R23.2, U10.6
/opto_coupler_channel4/FET-driver1/SIGNAL_IN: R27.2, U13.8
/opto_coupler_channel4/FET-driver2/SIGNAL_IN: R29.2, U13.6
/opto_coupler_channel5/FET-driver1/SIGNAL_IN: R33.2, U16.8
/opto_coupler_channel5/FET-driver2/SIGNAL_IN: R35.2, U16.6
/opto_coupler_channel/FET-driver1/SIGNAL_IN: R3.2, U1.8
/opto_coupler_channel/FET-driver2/SIGNAL_IN: R5.2, U1.6
CUR_MIRROR: Q14.1 (G), Q15.1 (G), Q16.1 (G), Q17.1 (G), Q18.1 (G), Q19.1 (G), Q20.1 (G), Q21.1 (G), Q22.1 (G), Q23.1 (G), Q24.1 (G), Q25.1 (G), Q26.1 (G), Q26.3 (D), U2.2 (GND)
GND: HUB75-1.4, HUB75-1.16, HUB75-2.4, HUB75-2.16, U1.2, U1.4, U4.2, U4.4, U7.2, U7.4, U10.2, U10.4, U13.2, U13.4, U16.2, U16.4
GNDD: C1.2, J1.1, J2.1, J3.1, J4.1, J5.1, J6.1, J7.1, J8.1, J9.1, J10.1, J11.1, J12.1, J13.1, Q14.2 (S), Q15.2 (S), Q16.2 (S), Q17.2 (S), Q18.2 (S), Q19.2 (S), Q20.2 (S), Q21.2 (S), Q22.2 (S), Q23.2 (S), Q24.2 (S), Q25.2 (S), Q26.2 (S), R37.2, R38.2, R39.2, R40.2, R41.2, R42.2, R43.2, R44.2, R45.2, R46.2, R47.2, R48.2, R49.2, U1.5, U1.7, U4.5, U4.7, U7.5, U7.7, U10.5, U10.7, U13.5, U13.7, U16.5, U16.7
GPIO1-1: HUB75-1.1, R1.1
GPIO1-2: HUB75-1.2, R2.1
GPIO1-3: HUB75-1.3, R7.1
GPIO1-4: HUB75-1.5, R8.1
GPIO1-5: HUB75-1.6, R13.1
GPIO1-6: HUB75-1.7, R14.1
GPIO2-1: HUB75-2.1, R19.1
GPIO2-2: HUB75-2.2, R20.1
GPIO2-3: HUB75-2.3, R25.1
GPIO2-4: HUB75-2.5, R26.1
GPIO2-5: HUB75-2.6, R31.1
GPIO2-6: HUB75-2.7, R32.1
unnamed: C1.1, D25.2 (A), Q13.1 (G), R37.1
unnamed: D1.2 (A), Q1.1 (G), R3.1, R4.2
unnamed: D2.1 (K), Q14.3 (D), R38.1
unnamed: D2.2 (A), J1.2, Q1.3 (D)
unnamed: D3.2 (A), Q2.1 (G), R5.1, R6.2
unnamed: D4.1 (K), Q15.3 (D), R39.1
unnamed: D4.2 (A), J2.2, Q2.3 (D)
unnamed: D5.2 (A), Q3.1 (G), R9.1, R10.2
unnamed: D6.1 (K), Q16.3 (D), R40.1
unnamed: D6.2 (A), J3.2, Q3.3 (D)
unnamed: D7.2 (A), Q4.1 (G), R11.1, R12.2
unnamed: D8.1 (K), Q17.3 (D), R41.1
unnamed: D8.2 (A), J4.2, Q4.3 (D)
unnamed: D9.2 (A), Q5.1 (G), R15.1, R16.2
unnamed: D10.1 (K), Q18.3 (D), R42.1
unnamed: D10.2 (A), J5.2, Q5.3 (D)
unnamed: D11.2 (A), Q6.1 (G), R17.1, R18.2
unnamed: D12.1 (K), Q19.3 (D), R43.1
unnamed: D12.2 (A), J6.2, Q6.3 (D)
unnamed: D13.2 (A), Q7.1 (G), R21.1, R22.2
unnamed: D14.1 (K), Q20.3 (D), R44.1
unnamed: D14.2 (A), J7.2, Q7.3 (D)
unnamed: D15.2 (A), Q8.1 (G), R23.1, R24.2
unnamed: D16.1 (K), Q21.3 (D), R45.1
unnamed: D16.2 (A), J8.2, Q8.3 (D)
unnamed: D17.2 (A), Q9.1 (G), R27.1, R28.2
unnamed: D18.1 (K), Q22.3 (D), R46.1
unnamed: D18.2 (A), J9.2, Q9.3 (D)
unnamed: D19.2 (A), Q10.1 (G), R29.1, R30.2
unnamed: D20.1 (K), Q23.3 (D), R47.1
unnamed: D20.2 (A), J10.2, Q10.3 (D)
unnamed: D21.2 (A), Q11.1 (G), R33.1, R34.2
unnamed: D22.1 (K), Q24.3 (D), R48.1
unnamed: D22.2 (A), J11.2, Q11.3 (D)
unnamed: D23.2 (A), Q12.1 (G), R35.1, R36.2
unnamed: D24.1 (K), Q25.3 (D), R49.1
unnamed: D24.2 (A), J12.2, Q12.3 (D)
unnamed: J13.2, JP1.1 (A), Q13.2 (S)
unnamed: R1.2, U1.1
unnamed: R2.2, U1.3
unnamed: R7.2, U4.1
unnamed: R8.2, U4.3
unnamed: R13.2, U7.1
unnamed: R14.2, U7.3
unnamed: R19.2, U10.1
unnamed: R20.2, U10.3
unnamed: R25.2, U13.1
unnamed: R26.2, U13.3
unnamed: R31.2, U16.1
unnamed: R32.2, U16.3
VDD: D1.1 (K), D3.1 (K), D5.1 (K), D7.1 (K), D9.1 (K), D11.1 (K), D13.1 (K), D15.1 (K), D17.1 (K), D19.1 (K), D21.1 (K), D23.1 (K), D25.1 (K), JP1.2 (B), Q1.2 (S), Q2.2 (S), Q3.2 (S), Q4.2 (S), Q5.2 (S), Q6.2 (S), Q7.2 (S), Q8.2 (S), Q9.2 (S), Q10.2 (S), Q11.2 (S), Q12.2 (S), Q13.3 (D), R4.1, R6.1, R10.1, R12.1, R16.1, R18.1, R22.1, R24.1, R28.1, R30.1, R34.1, R36.1, U2.1 (VDD)

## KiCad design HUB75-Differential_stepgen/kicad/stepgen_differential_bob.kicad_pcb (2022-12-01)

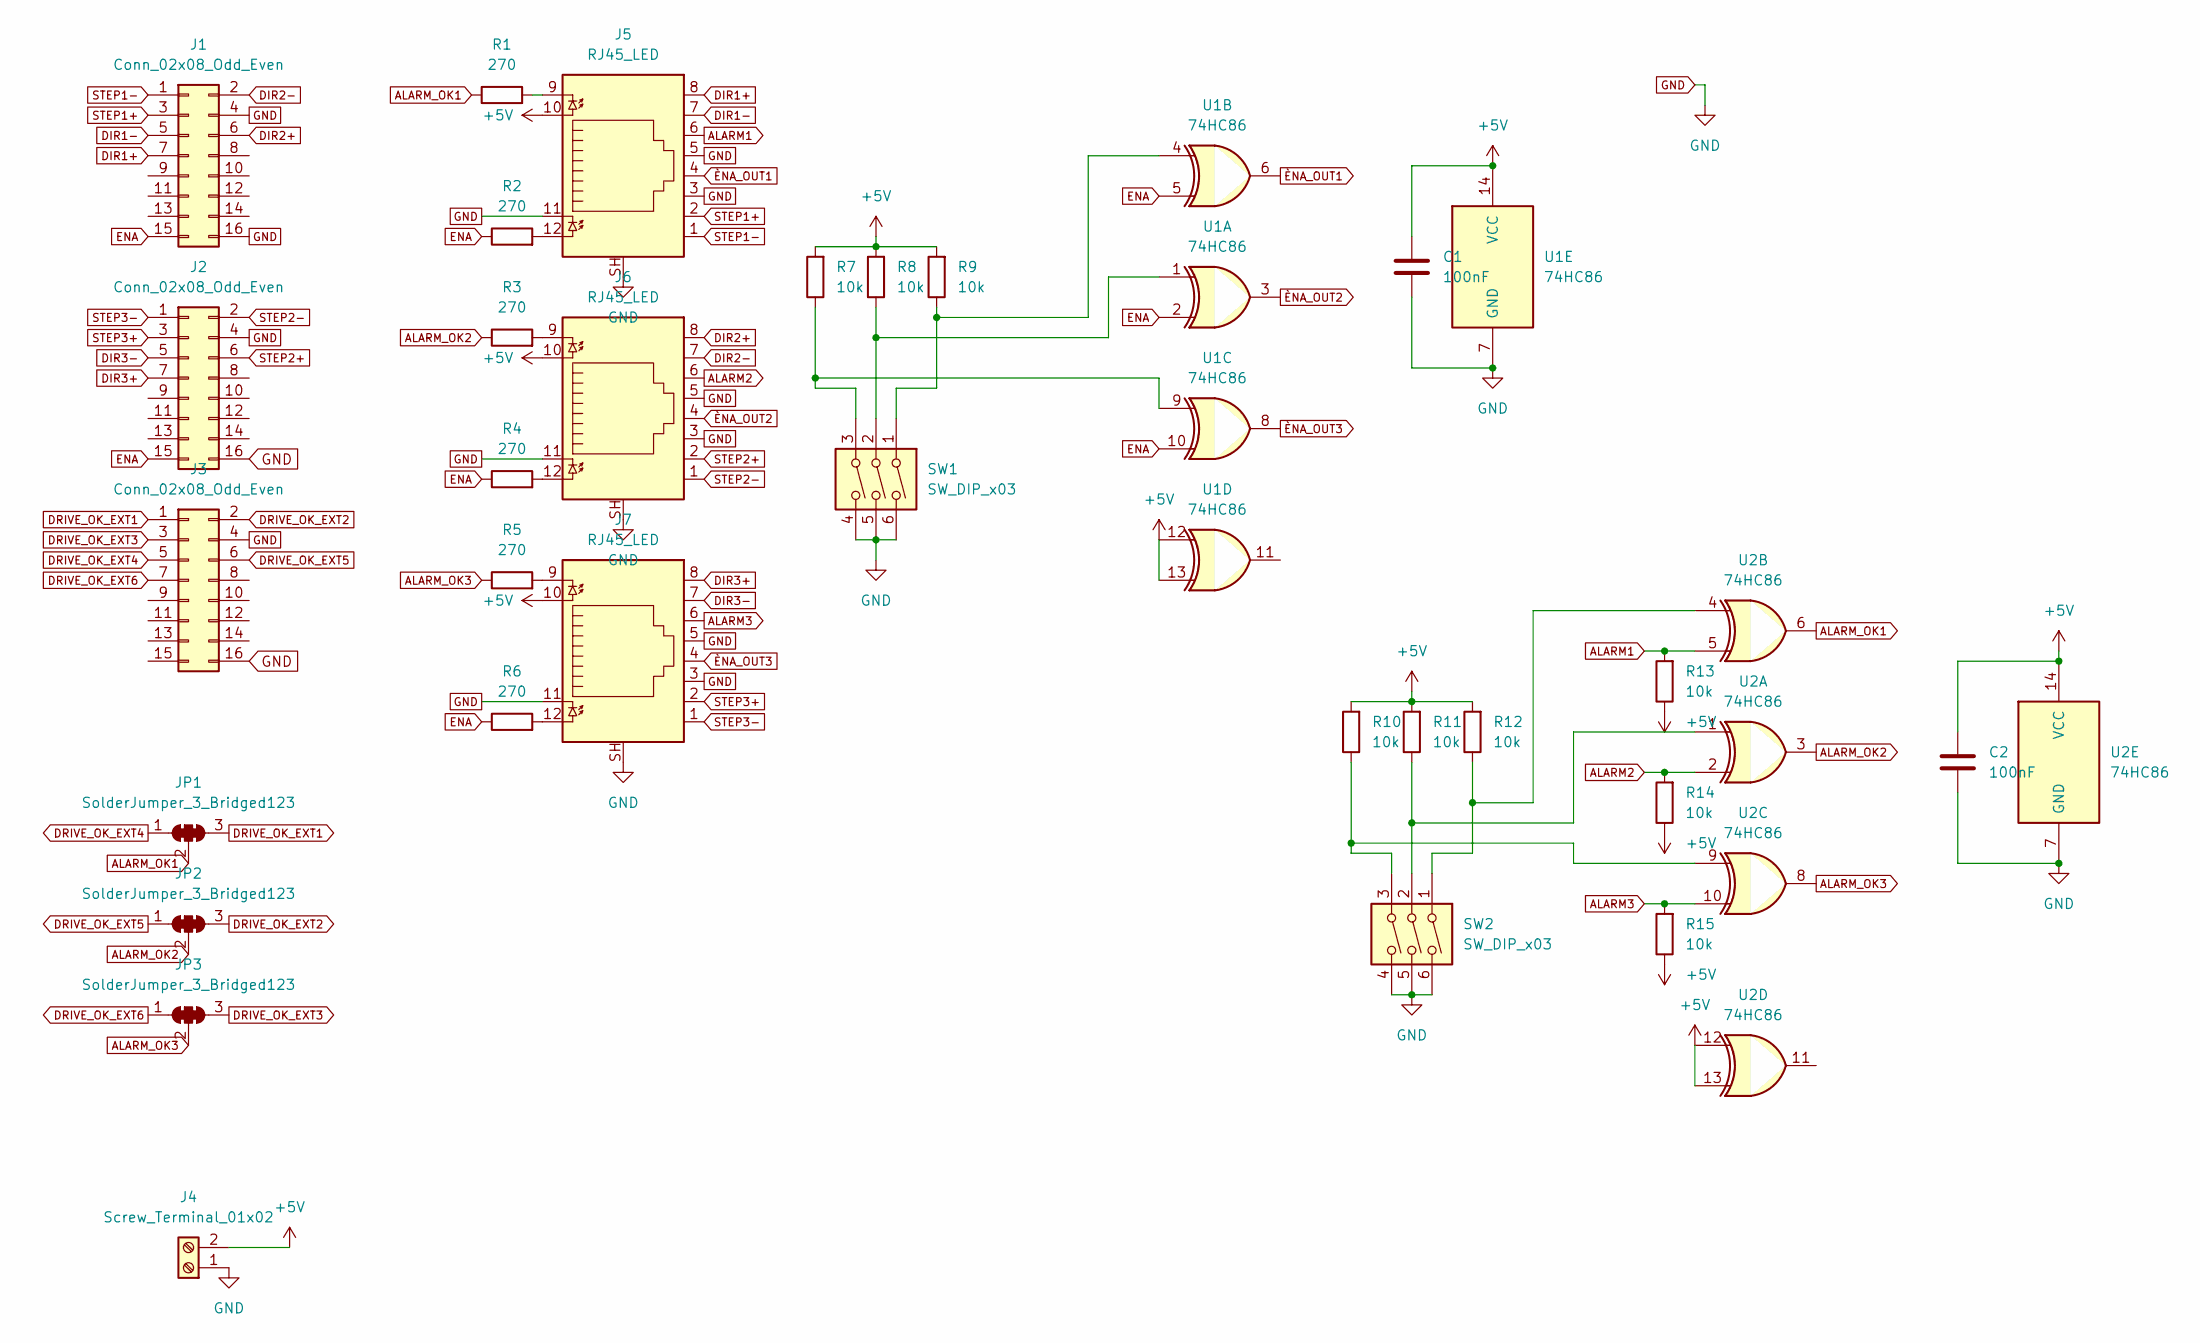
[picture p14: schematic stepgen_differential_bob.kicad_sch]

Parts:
C1, C2: 100nF; C_1206_3216Metric_Pad1.33x1.80mm_HandSolder
J1, J2, J3: Conn_02x08_Odd_Even; IDC-Header_2x08_P2.54mm_Vertical
J4: Screw_Terminal_01x02; TerminalBlock_Phoenix_PT-1,5-2-3.5-H_1x02_P3.50mm_Horizontal
J5, J6, J7: RJ45_LED; RJ45_BEL_SS74301-00x_Vertical
JP1, JP2, JP3: SolderJumper_3_Bridged123; SolderJumper-3_P2.0mm_Open_TrianglePad1.0x1.5mm_NumberLabels
R1, R2, R3, R4, R5, R6: 270; R_1206_3216Metric_Pad1.30x1.75mm_HandSolder
R7, R8, R9, R10, R11, R12, R13, R14, R15: 10k; R_1206_3216Metric_Pad1.30x1.75mm_HandSolder
SW1, SW2: SW_DIP_x03; DIP-6_W7.62mm
U1, U2: 74HC86; SO-14_5.3x10.2mm_P1.27mm

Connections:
+5V: C1.1, C2.1, J4.2, J5.10, J6.10, J7.10, R7.2, R8.2, R9.2, R10.2, R11.2, R12.2, R13.1, R14.1, R15.1, U1.12, U1.13, U1.14 (VCC), U2.12, U2.13, U2.14 (VCC)
ALARM1: J5.6, R13.2, U2.5
ALARM2: J6.6, R14.2, U2.2
ALARM3: J7.6, R15.2, U2.10
ALARM_OK1: JP1.2 (C), R1.1, U2.6
ALARM_OK2: JP2.2 (C), R3.1, U2.3
ALARM_OK3: JP3.2 (C), R5.1, U2.8
DIR1+: J1.7, J5.8
DIR1-: J1.5, J5.7
DIR2+: J1.6, J6.8
DIR2-: J1.2, J6.7
DIR3+: J2.7, J7.8
DIR3-: J2.5, J7.7
DRIVE_OK_EXT1: J3.1, JP1.3 (B)
DRIVE_OK_EXT2: J3.2, JP2.3 (B)
DRIVE_OK_EXT3: J3.3, JP3.3 (B)
DRIVE_OK_EXT4: J3.5, JP1.1 (A)
DRIVE_OK_EXT5: J3.6, JP2.1 (A)
DRIVE_OK_EXT6: J3.7, JP3.1 (A)
ENA: J1.15, J2.15, R2.1, R4.1, R6.1, U1.2, U1.5, U1.10
GND: C1.2, C2.2, J1.4, J1.16, J2.4, J2.16, J3.4, J3.16, J4.1, J5.3, J5.5, J5.11, J5.SH, J6.3, J6.5, J6.11, J6.SH, J7.3, J7.5, J7.11, J7.SH, SW1.4, SW1.5, SW1.6, SW2.4, SW2.5, SW2.6, U1.7 (GND), U2.7 (GND)
unnamed: J5.9, R1.2
unnamed: J5.12, R2.2
unnamed: J6.9, R3.2
unnamed: J6.12, R4.2
unnamed: J7.9, R5.2
unnamed: J7.12, R6.2
unnamed: R7.1, SW1.3, U1.9
unnamed: R8.1, SW1.2, U1.1
unnamed: R9.1, SW1.1, U1.4
unnamed: R10.1, SW2.3, U2.9
unnamed: R11.1, SW2.2, U2.1
unnamed: R12.1, SW2.1, U2.4
STEP1+: J1.3, J5.2
STEP1-: J1.1, J5.1
STEP2+: J2.6, J6.2
STEP2-: J2.2, J6.1
STEP3+: J2.3, J7.2
STEP3-: J2.1, J7.1
ÈNA_OUT1: J5.4, U1.6
ÈNA_OUT2: J6.4, U1.3
ÈNA_OUT3: J7.4, U1.8

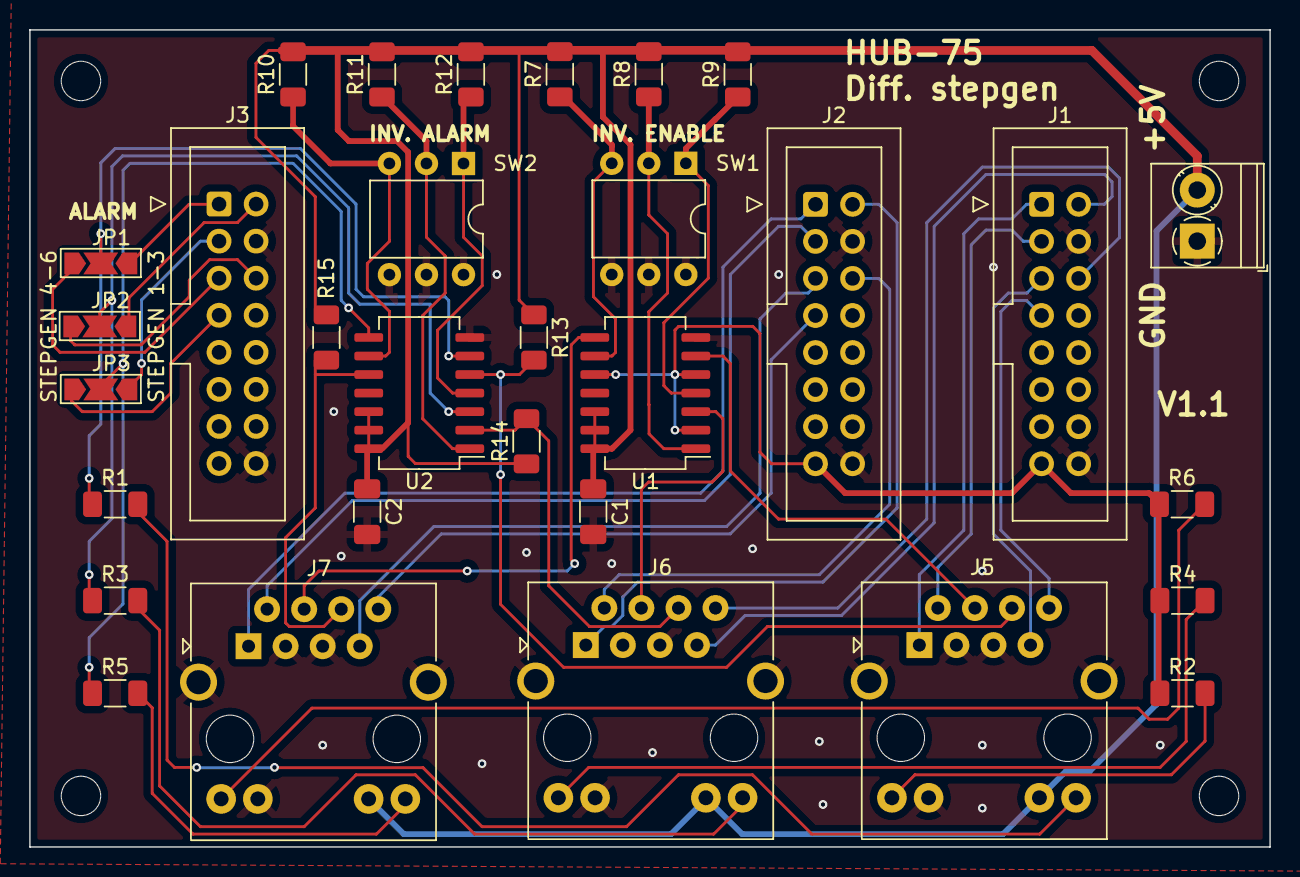
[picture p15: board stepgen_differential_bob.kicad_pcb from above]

Board: 2 copper layers, 85.0 x 56.0 mm, 35 parts (0 on the bottom side), 42 nets.

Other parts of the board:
Hole1, Hole2, Hole3, Hole4: MountingHole_2.7mm_M2.5_DIN965

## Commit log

2022-11-15 Add changing board
2022-11-16 Proto-type production ready
    [hub75_sourcing_output.kicad_pcb]
2022-11-16 Moved license logo + added name
    [hub75_sourcing_output.kicad_pcb]
2022-11-17 Update board with current mirror + backup
    [FET-driver.kicad_sch, hub75_sourcing_output.kicad_pcb, hub75_sourcing_output.kicad_sch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]
2022-11-17 Update label
    [FET-driver.kicad_sch, hub75_sourcing_output.kicad_pcb, hub75_sourcing_output.kicad_sch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]
2022-11-17 Production files v1.0
    [bom.csv, designators.csv, positions.csv]
2022-11-17 Update part number
    [bom.csv, hub75_sourcing_output.kicad_sch]
2022-11-17 Remove incorrect GND connection
    [FET-driver.kicad_sch, hub75_sourcing_output.kicad_sch, opto_coupler_channel.kicad_sch]
2022-11-17 Smaller resistors + production ready
    [bom.csv, designators.csv, positions.csv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]
2022-11-20 Change trace width
    [stepgen_differential_bob.kicad_pcb]
2022-11-20 Moved design to correct folder
    [HUB75-Sinking_input.kicad_pcb, HUB75-Sinking_input.kicad_sch, optocoupler_channel.kicad_sch]
2022-11-20 Update BOM and images
2022-11-20 Added production files
    [bom.csv, designators.csv, positions.csv]
2022-12-01 Corrected part list
    Added missing decoupling capacitors
    Corrected serial number of the XOR-gate
2022-12-01 Update to v1.1 after prototype
    [bom.csv, positions.csv, stepgen_differential_bob.kicad_pcb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]
2022-12-01 New render with IDC-connectors
2022-12-02 New version after prototype failed
    [FET-driver.kicad_sch, bom.csv, designators.csv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]
2022-12-02 Version for prototype
    [HUB75-Sinking_input.kicad_pcb, HUB75-Sinking_input.kicad_sch, bom.csv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]

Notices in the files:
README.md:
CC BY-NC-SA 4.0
